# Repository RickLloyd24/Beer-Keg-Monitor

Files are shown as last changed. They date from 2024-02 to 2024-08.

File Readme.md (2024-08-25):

# Beer Keg Monitoring System

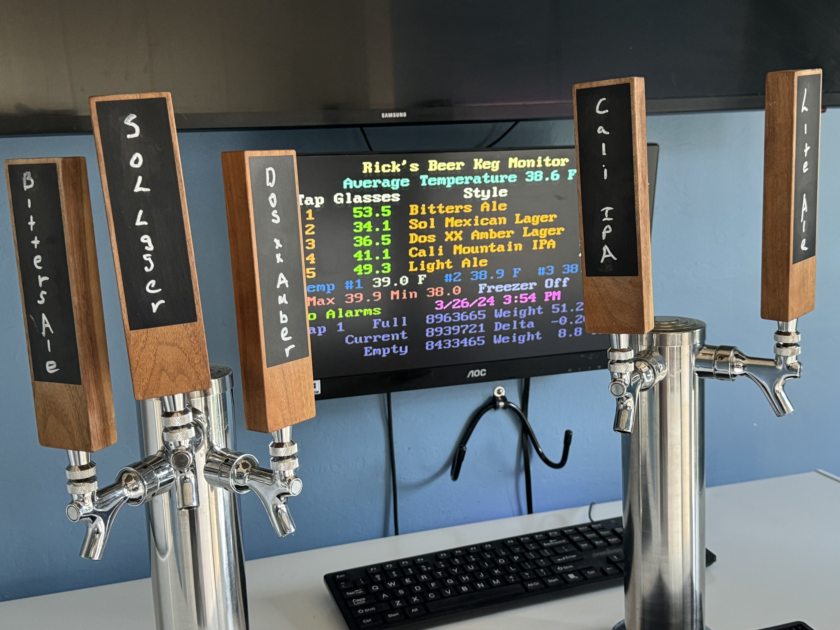
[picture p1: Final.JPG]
Build your own beer keg monitoring system that keeps track of how many
glasses of beer are left in each keg. The entire system costs less than
\$100 for 5 beer taps.

## Features:

- Tracks number of glasses of beer left.

- Controls Beer freezer temperature

- Monitors up to 8 beer taps.

- Temperature Stability +/- 0.75 degrees F

- Works with all DHT,  MCP9808 and/or DS18B20 Temperature Sensors

- - Up to 3 temperature sensors can be used.

- #NEW# Gets Time of day via WiFi and Network Time Protocol

- #NEW# Added CO2 Saver Support (See CO2 Saver Project)

- #NEW# Provides Redundant Power Supply Support

## Introduction

Currently there are two types of systems to measure how much beer is
left in the keg:

1) Flow measuring.

2) Weight of Keg.

Flow measuring systems are cheaper (6 taps about \$500) but they have
limited utility and you have to clean them every time you clean your
beer lines (every 6 weeks).

Weight of keg systems are none intrusive, but very expensive (\$1000 for
5 taps). They are not integrated with your entire system. This system
measures the weight of the keg but is low cost.

## Bill of Materials

The following is the bill of Materials for the entire system:

| Item | Qty | Description | Price | Total |
| ---- | --- | --- | --- | --- |
| 1 | 5 | Scale Plate | \$ 2.50  | \$ 12.50 |
| 2 | 5 | HX711 Load Cell Amplifier | \$ 2.00  | \$ 10.00 |
| 3 | 20  | Load Cell | \$ 0.80  | \$ 16.00 |
| 4 | 1 | PS2 Keyboard | \$ 5.00  | \$ 5.00  |
| 5 | 1 | VGA Monitor | \$ 10.00 | \$ 10.00 |
| 6 | 2 | DHT 22/AM2302 Sensor | \$ 3.33  | \$ 6.67  |
| 7 | 1 | ESP32 Breakout Board | \$ 13.00 | \$ 13.00 |
| 8 | 1 | ESP32 Development Board | \$ 8.50  | \$ 8.50  |
| 9 | 1 | VGA Breakout Board | \$ 7.50  | \$ 7.50  |
| 10 | 1 | PS2 Breakout Board | \$ 4.00  | \$ 4.00  |
| 11 | 1 | Relay | \$ 2.00  | \$ 2.00  |
| | | Total | | \$ 95.17 |

<style>
</style>

## Tools Required

- Soldering Iron (Amazon $10, Soldering Iron Kit - 9-in-1 With 5 Tips, Solder Wire)

- Connectors and Crimping Tool (Amazon $30, Kit with 1550PCS Male and Female 2.54mm Terminals)

- Multi Meter (Recommended Harbor Freight $7, 7-Function Digital Multimeter)

- Drill Motor

- Small Pliers, screw drivers

The following figure is a high level over of the whole project:

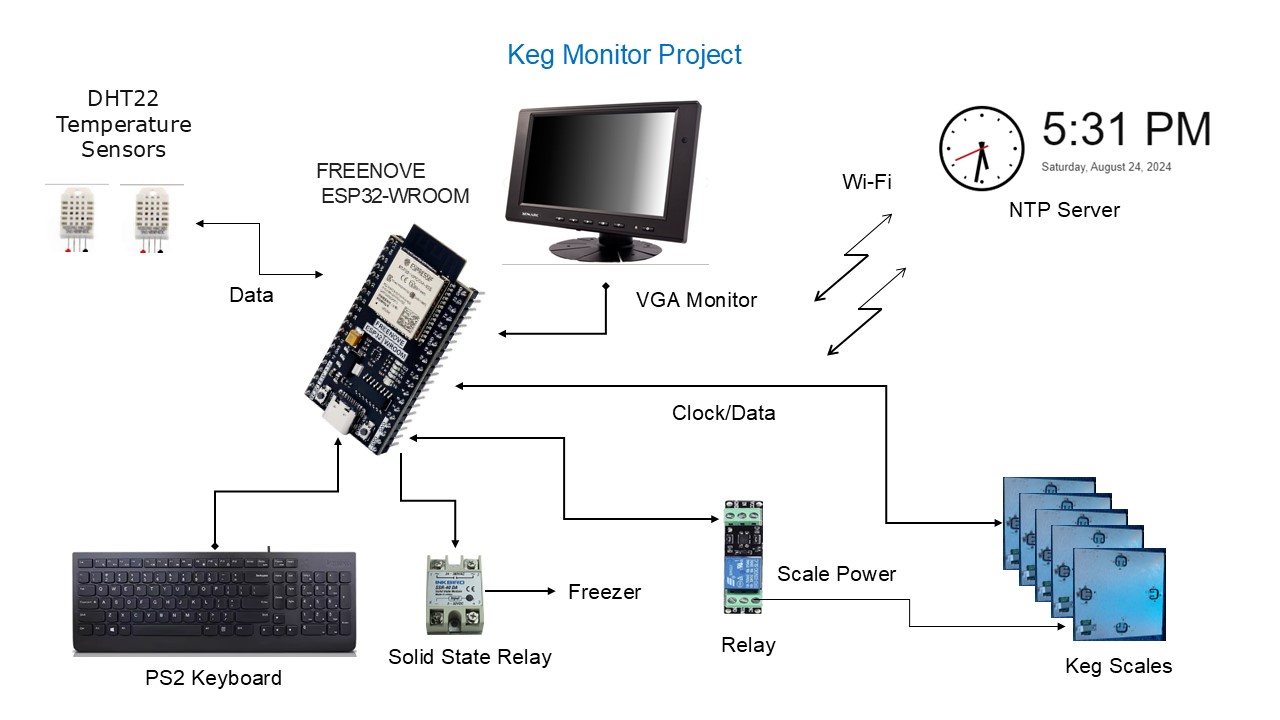
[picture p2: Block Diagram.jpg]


The data is displayed on the VGA monitor and input is via the keyboard.  A Solid State Relay (SSR) is used to control the freezer.  I replaced a standard relay with a SSR.  This relay is much more reliable and supports higher currents.  Upto  3 different temperature sensors can be used.  The time of day is received via Wi-Fi from an NTP Server.  A scale power relay is used to reduce false scale readings (discussed later).

## Theory of Operation

The theory of operation is quite simple. The data you need is:

1) Scale reading with nothing on the scale (Empty Scale Quanta)

2) Scale reading with a full keg of beer on the scale (Full Scale
   Quanta)

3) Scale reading of current keg (Current Scale Quanta)

4) Weight of a full keg (Full Keg Weight)

5) Weight of an empty keg (Empty Keg Weight)

The system automatically measures the first three items, all you need to
do is measure the full key weight and the empty keg weight. I just use a
bathroom scale.

Reading Per Ounce = (Full Scale Quanta – Empty Scale Quanta) / (Full Keg
Weight \* 16)

Current Ounces = (Current Scale Quanta – Empty Scale Quanta) / Reading
Per Ounce

Glasses = (Current Ounces – Empty Keg Weight) / 12 Ounces per glass

## Software

The software is in the software folder. 

## Hardware

Check out the hardware folders for all the intimate hardware details.

## Why a Keezer?

A Keezer is a chest **Freezer** converted to a **Kegerator** which is
commonly called a Keezer.

A Keezer has many advantages:

- They are more energy efficient.

- They have a lot of space for the cost.

- It is easy to access all the keg connectors.

- It is easy to install and remove the kegs.

Most freezers are not tall enough for the kegs with the fittings, so you
need to install a frame (collar) between the freezer top and the freezer
base. This is not very hard. You can find lots of articles on the
internet that describe how to do this.

The advantage of the collar is you do not have to drill through the wall
of the freezer to install taps, risking hitting a freezer coil. You can
also drill through the collar to bring in and out wires.

You should insulate the kegs from the bottom of the freezer to prevent
the beer from freezing and protect the bottom of the freezer. I used
padded vinyl plank flooring which worked great.

## Lessons Learned

1) Buy solid wire instead of stranded.  Much easier to work with.

2) Use an Ohm meter to check everything out.  It can save a lot of
   troubleshooting time. You can get one at Harbor Freight for just a
   few dollars. 

3) Buy the ESP32 Development Boards, instead of the UNO form factor
   boards (i.e. ESP32 D1 R32 or ESP8266 D1 R2).  Much easier to work
   with, better Wi-Fi, and faster.

4) If you need a lot of memory and pins use the ESP32-S3 development
   boards.

5) Use breakout boards with screw terminals, much easier and more
   reliable than the solder boards.

## HX711 Scale Sensor

I had a lot of trouble with the HX711 ADC sensor changing state. Periodically The scale reading would change to a completely different number and stay in this state. The readings were still very consistent in this false state. Powering the system On/Off would restore the HX711 ADC to the correct state.

I was able to determine the cause of this problem was power transients. I confirmed this by powering the scales from a battery for several days and no transients occurred.

To fix this problem a scale power relay was added. Every time the freezer is turned On/Off or the CO2 solenoid is turned On/Off the scales are powered off before the event. After the event the scales are powered back on. This finally solved the problem.

The other advantage of this solution is, if another source caused the power transient, the scales will eventually be turned Off/On and read the correct value.

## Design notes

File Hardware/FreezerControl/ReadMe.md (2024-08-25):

# Freezer Control Relay

The Freezer Control Relay is used to turn On/Off the freezer.

## **Relay Specifications**

The following are the specifications for the relay.

- Input: DC 3-32V;
- Output: AC 24-380V, 40 amps
- Number of switches: Infinite

The relay supports currents up to 40 amps and the relay activation works down to 3 volts.  A GPIO output can be used to drive the relay. The approximate current at 3.3 volts is 8.5 milliamps. The maximum drive current for an ESP32 GPIO is 40 ma, with 20 ma recommended maximum. So, this relay is a good, reliable choice. The SSR also has a resistance of about 3 ohms with a 3.3-volt drive that reduces the surge current.

The freezer I use was an Insignia™ - 10.2 Cu. Ft. Chest Freezer. The startup current is 21.4 amps and the on current is 2.0 amps. This relay has handled the startup current fine. 

Initially I used a small 10-amp relay. The relay failed in the "On" state after about 6 months which froze my beer.  I think because of the high inrush current.  A mechanical relay has a life expectancy of about 1 million activations. Under normal operation as a freezer controller the relay will last about 5 - 7 years. However, Solid State Relays (SSR) have an infinite number of switches. A SSR will not last forever, but it fails for reasons other than switching.I strongly recommend the SSR relay because it is more robust and more reliable. You may also consider the redundant relay that I talk about in the next section.

## **Schematic**

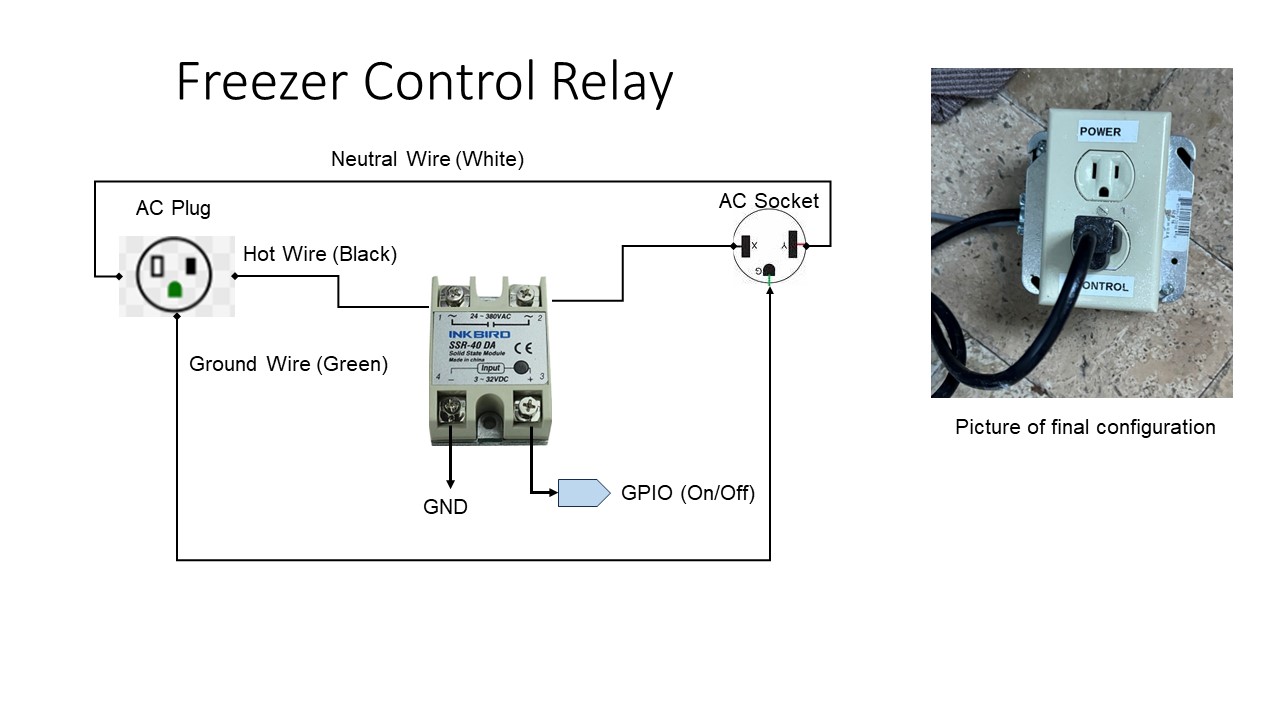
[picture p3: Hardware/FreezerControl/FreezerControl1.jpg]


The above schematic provides an overview of the connections. I included a picture of my final product. I got the line cord off a food blender that was broken. The line cord has 16-gauge wires.  The plug and the box were pieces I had laying around. The relay is enclosed inside the electrical box. The plug in the box goes to the freezer.  

## **Redundant Relay Configuration**

### **Background**

SSRs can fail in either the open or closed position. Since I have about $500 worth of beer in my freezer, I wanted a redundant relay that would still work if the primary relay failed in either the open or closed position. the following describes my solution.

## **Overview**

The redundant relay concept is shown in the following figure:\

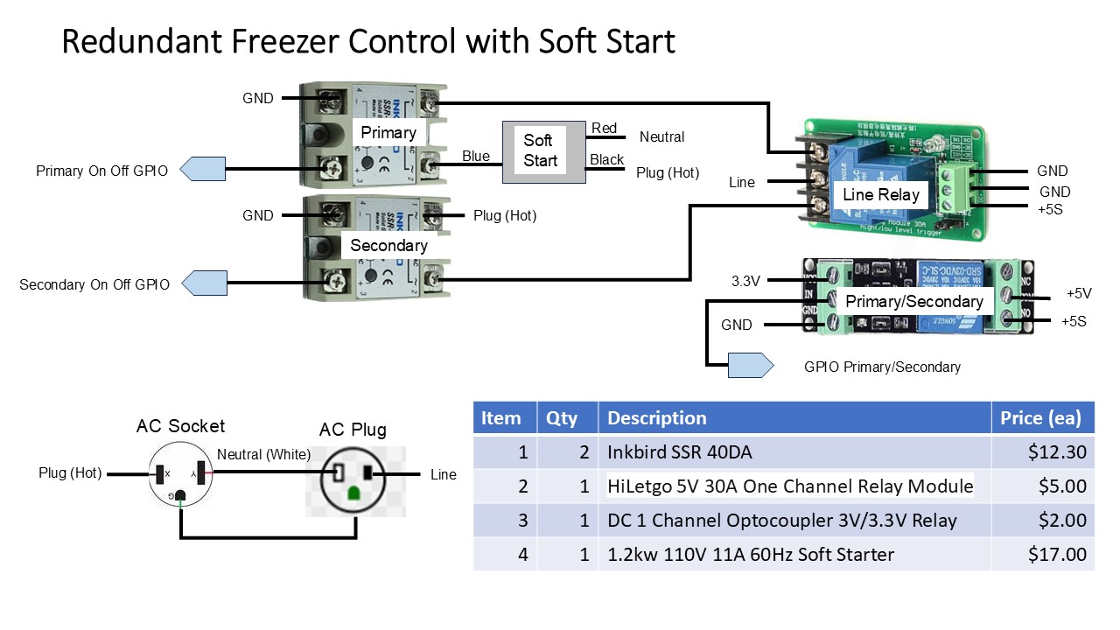
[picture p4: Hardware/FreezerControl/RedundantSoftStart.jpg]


There are primary and secondary circuits in the design. When primary is on (LOW) no components are powered on when the freezer is Off.  When the Primary GPIO On/Off signal is HIGH the SSR switches on. The current drain is about 8.7 ma, which is about half of the  recommended maximum. The GPIO On/Off signal is HIGH about 25% of the time in the summer.

A switch to the secondary circuit occurs when the freezer temperature is below 32 degrees or above 40 degrees. Once switched to the secondary the only way to get back to primary is to reset the ESP32 board or enter a command.

The switch to Secondary only occurs when the GPIO On/Off signal is in the off position, so no AC current is flowing. When the GPIO Primary/Secondary signal goes HIGH, the Primary/Secondary relay activates the +5S signal which activates the Line Relay. The line relay now sends the AC power to the secondary SSR. When the secondary circuit is active the Secondary On/Off GPIO signal is used.  I wanted a relay with big contacts for the Line Relay and I could not find one that worked on 3.3 volts. The Primary/Secondary relay is included just to provide 5 volts to the Line Relay. You can eliminate the Primary/Secondary relay if you want to use a 10 amp relay.

The Secondary circuit is tested everytime I need to change a keg in the freezer or I clean the beer lines.  That way I know the Secondary circuit is good.  After the freezer gets back to the desired temperature, I switch back to Primary.  You can tell which circuit is active on the main display.  There is either a "P" or "S" next to the freezer status.

This diagram includes a soft start circuit to reduce the freezer on current.  It seemed to help some but I am not sure it is worth the extra cost and is another component that can fail.

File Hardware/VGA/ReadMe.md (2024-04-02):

# VGA Interface

For this project I selected a VGA monitor for my local display. VGA monitors
are large and easy to read for my guests. They are also readily available and
cheap. I got mine free at a garage sale. They were closing up and the monitor
was still there, so they gave it to me. I also bought a VGA monitor at a thrift
store for 10 dollars.

## VGA Interface Schematic

The following is the schematic for the VGA interface:

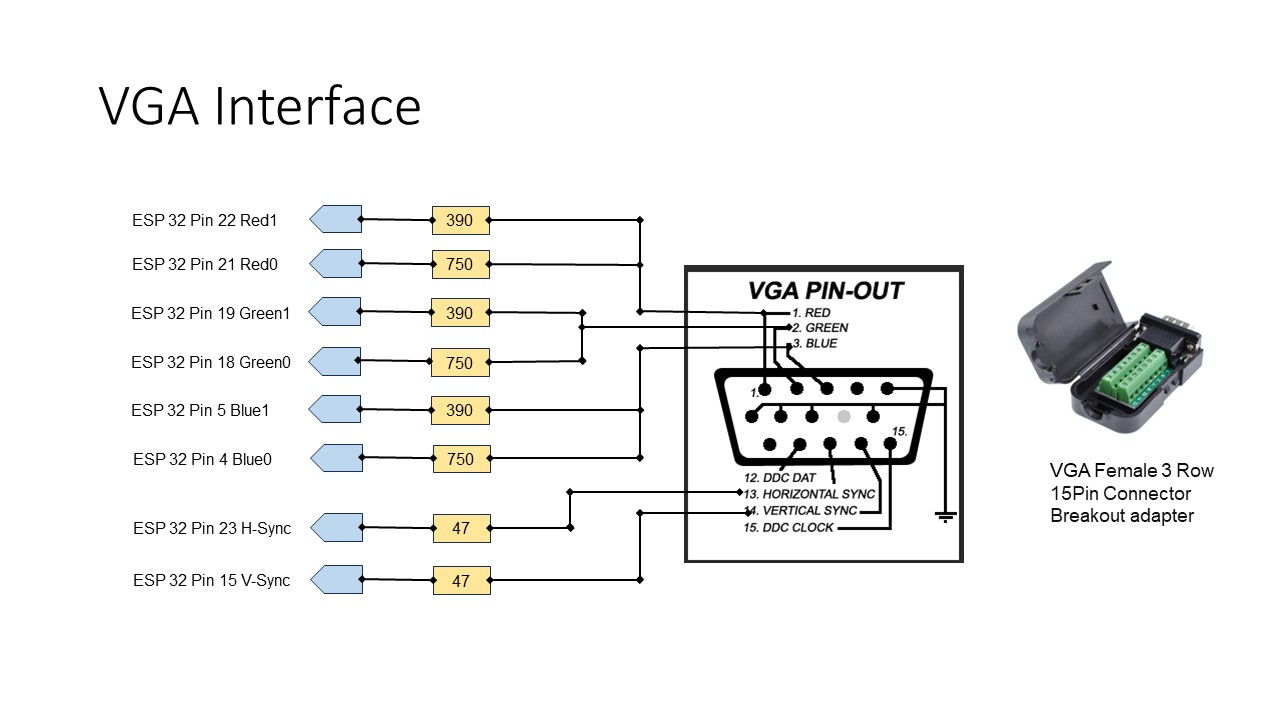
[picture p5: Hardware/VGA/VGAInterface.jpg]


The resistors for the RGB signals should have approximately a  2 to 1 ratio. The 47-ohm resistors are for impedance matching.

With this configuration you get 64 colors. 

## Software

For this project I used the FabGL Graphics Library for ESP32.  This library is great!  I used the same library for my keyboard interface.  The library overview is at the following link  [www.FabGL.com](http://www.fabgl.com/)  and is also available on Github.  I used the default pin numbers as defined in the library.

There is a **VGATest** program that displays all 64 colors and can help you test the VGA interface.  The following is a sample of the test display showing all 64 colors.

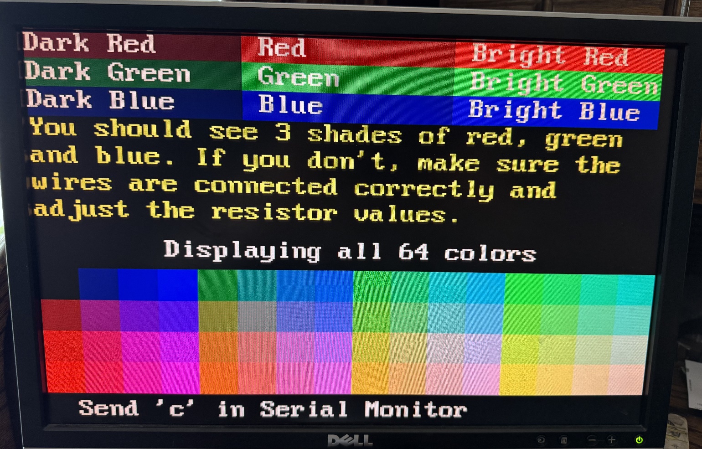
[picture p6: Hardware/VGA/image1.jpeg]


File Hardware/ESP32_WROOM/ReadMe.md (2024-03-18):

# **FREENOVE ESP32-WROOM Board**

For this project I selected the FREENOVE ESP32-WROOM developement board.  The main reason is the breakout board that is available for this board.  The breakout board is great.  I prefer to use a Arduino power supply instead of powering board from a type C USB connector.

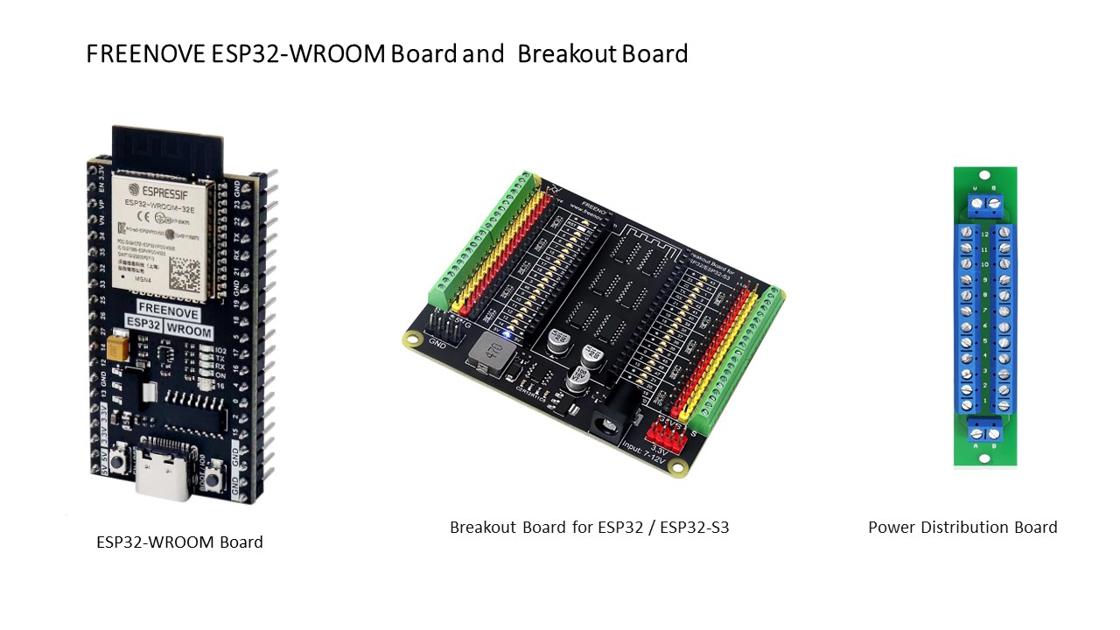
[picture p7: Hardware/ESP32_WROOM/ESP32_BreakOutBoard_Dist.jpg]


## ESP32 Breakout Board

Breakout Board Features:

- •Compatible models -> Freenove ESP32 / ESP32-S3 series. (Note: Boards from other brands are not compatible due to different pinout.)

- •GPIO status LED -> LED on if GPIO outputs/inputs high level, LED off if GPIO
  outputs/inputs low level.

- •Independent LED -> The status LED is driven by the chip instead of the GPIO so the GPIO will not be affected.

- •Power circuit -> Provide multiple 5V and 3.3V power outputs. (5V output up to 3A
  with external power supply.)

- •Terminal block and header -> Connect to all GPIO headers 

## ESP32-WROOM

The ESP Development board has:

- 32 bit processor that runs at 240 MHz

- 4 MB Flash and 520 KB of SRAM running at 80 MHz

- Wi-Fi and Bluetooth Interfaces

- Onboard RGB LED and Green LED

- Onboard Code Uploader

The ESP32 includes

- 8 Analog-to-Digital Converter (ADC) channels

- 3 SPI interfaces

- 3 UART interfaces

- 2 I2C interfaces

- 16 PWM output channels

- 2 Digital-to-Analog Converters (DAC)

- 2 I2S interfaces

- 10 Capacitive sensing GPIOs

The ADC (analog to digital converter) and DAC (digital to analog converter) features are assigned to specific static pins. However, you can decide which pins are UART, I2C, SPI, PWM, etc – you just need to assign them in the code. This is possible due to the ESP32 chip’s multiplexing feature.

## Power Distribution Board

I use these boards for my 3.3 Volt power and ground distribution.  There are not enough pins the ESP32 for all the power and ground signals.  These little boards make distributing the power and ground very easy.

## FREENOVE ESP32 Pin Out

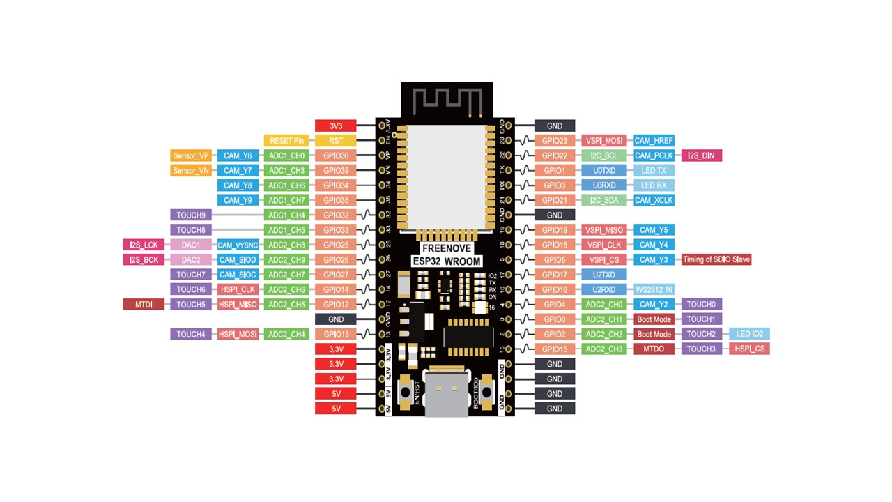
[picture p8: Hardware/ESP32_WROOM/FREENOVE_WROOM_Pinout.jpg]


##

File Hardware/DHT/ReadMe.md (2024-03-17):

# DHT22/AM2302

The Digital Humidity and Temperature (DHT)  Sensor Module is compact and easy to use module.  

## Features:

- Main Chip: AOSONG AM2302 High Sensitive Temperature Humidity Sensor
- Single-bus digital signal output, bidirectional serial data
- Temperature range: -40 to 80 degree celsius, 
- Temperature measurement accuracy: +/- 0.5℃ degree celsius
- Humidity measuring range: 0~100%RH, 
- Humidity measurement accuracy: ±2%RH

## Specifications

- Power supply 3.3-6V DC

- Sensing element Polymer capacitor

- Operating range humidity 0-100%RH; temperature -40~80 Celsius

- Accuracy humidity +-2%RH(Max +-5%RH); temperature <+-0.5 Celsius

- Resolution or sensitivity humidity 0.1%RH; temperature 0.1 Celsius

- Repeatability humidity +-1%RH; temperature +-0.2Celsius

- Humidity hysteresis +-0.3%RH

- Long-term Stability +-0.5%RH/year

- Sensing period Average: 2 seconds

## Software

The software will work with any DHT sensors (DHT11, DHT21, DHT22, AM2301, or AM2302). You can use upto 3 sensors (any mix of MCP9808 and DHT sensors). The "constants.h" file is edited to select the number of sensors and the type of sensors used.

I tried multiple DHT sensor libraries.  They either were unreliable (sensor temperature got stuck) or they were blocking which caused the display to blink when the sensor was read.  To solve this problem I wrote my own library <DHTSimple.h>.  This library is avalible on GitHub.

The DHT sensors can be connected to available GPIO pin.  The pin numbers are defined in the "constants.h" file.  If MCP9808 sensors are installed, the sensor numbers will be assigned to these devices first.

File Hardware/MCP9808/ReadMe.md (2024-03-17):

# MCP9808 Precision Temperature Sensor

This MCP9808 digital temperature sensor is low cost temperature sensor with a typical accuracy of ±0.25°C over the sensor's -40°C to +125°C range and precision of +0.0625°C.   It has a wide voltage range of 2.7  to 5.5 volts.  You can typically buy them for about 6 dollars.   The following is a picture of the typical device.  The device works on the I2C bus that is explained in the next section.

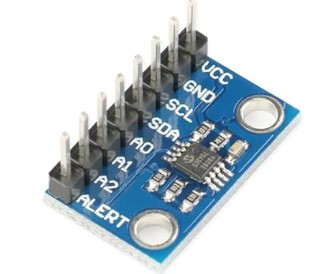
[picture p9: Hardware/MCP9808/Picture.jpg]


## I2C Bus

The I2C bus is a standard **bidirectional interface** that uses a controller, known as the master, to communicate with slave devices. A slave may not transmit data unless it has been addressed by the master. Each device on the I2C bus has a specific device address to differentiate between other devices that are on the same I2C bus.  The I2C bus can support 255 different addresses with a two wire interface.

All Arduino compaitible boards support the I2C bus.  The MCP9808 has 3 address pins so you can connect up to 8 on the I2C bus.  The base address 0x18.

The I2C bus is supported by the Arduino Wire library.

## MCP9808 vs DHT Sensors

I decided to add the capability to use either Digital Humidity and Temperature (DHT) or  MCP9808 sensors.  I found that the DHT22 sensors had temperature biases upto 2 degrees and they seem to drift.    The following figure compares the MCP to the DHT22.

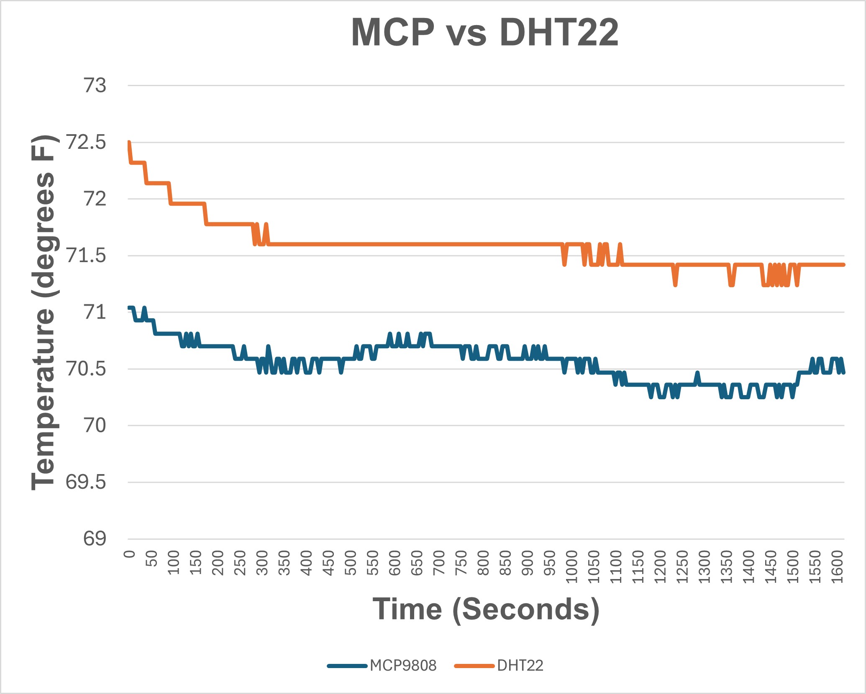
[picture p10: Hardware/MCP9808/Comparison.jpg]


## Implementation

I ran five wires to each sensor (+3.3V, Gnd, SDA, SCL and A0).  On one sensor A0 was connected to 3.3V and the other sensor is connected to GND.  The addresses of the two sensors are hard wired to 0x18 and 0x19.  The following is a picture of the wired sensors.  I found that the ground wire had to be run to 0x18 sensor (sensor #1) to get reliable readings.  In the picture these sensors are generic sensors.  On Adafruit sensors the Alert pin is where the A0 pin is.  For the Adafruit sensors I used a 4 pin connector and ran a single wire to the A0 address line.

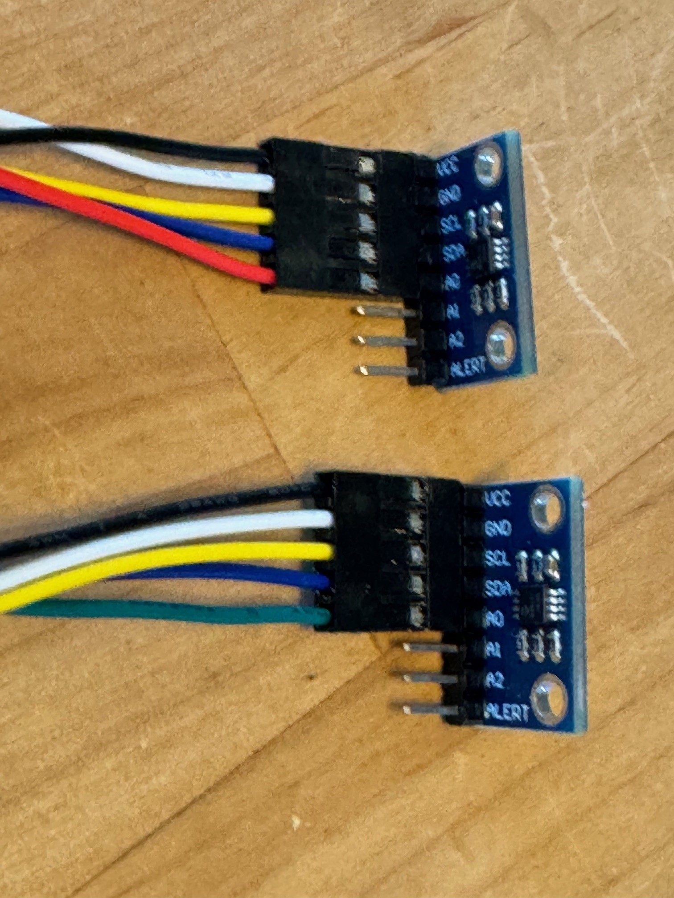
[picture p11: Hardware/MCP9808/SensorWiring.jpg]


Because the IC2 bus runs at a high rate (100 kHz)  the SDA and SCL wires should be kept to about a foot or less.  The other wires can be longer.

## Software

You can use upto 3 sensors (any mix of MCP9808 and DHT sensors). The "constants.h" file is edited to select the number of sensors and the type of sensors used.

The SDA and SCL pins are also defined in the "constants.h" file.  The SCL pin is 13 and the SDA pin is 14, but these can be assigned to almost any GPIO pin.

The MCP9808 sensors are assigned sensor numbers first.  For example if you have 2 MCP9808 sensors and 1 DHT sensor, Sensor #1 and Sensor #2 are the MCP9808 and Sensor #3 is the DHT sensor.

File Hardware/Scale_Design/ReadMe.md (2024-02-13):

# Scales

For the scale plate I used Aluminum Composite Sign Panel sheet.  The sheets are 1/8 inch thick and come in a variety of sizes.  The most common is 12 inches by 24 inches.  You can use standard wood cutting tools to work with the plates.



I made two sizes of scale plates.  9.25 inches for Corny and 1/6 Barrel kegs. 12.125 for the Slim 1/4 Barrel.

## Schematic

The following is a schematic for one load cell:

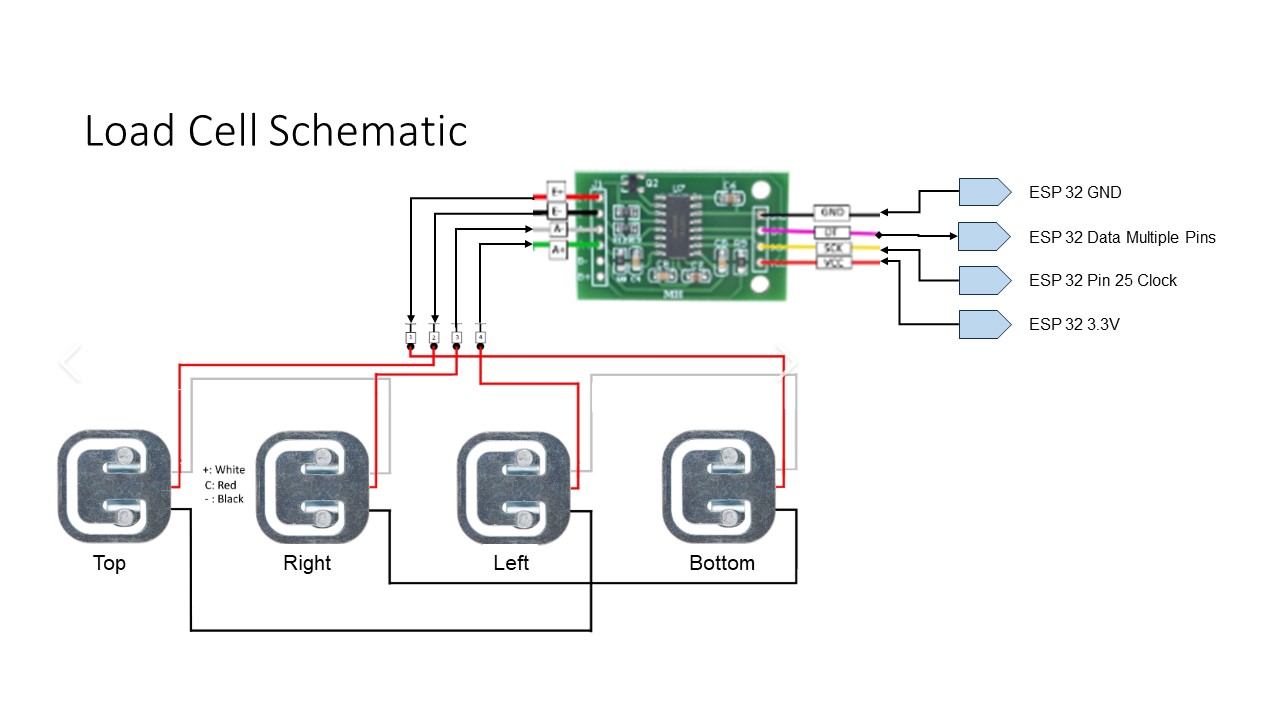
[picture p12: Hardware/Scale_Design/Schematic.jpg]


The following is the Schmatic for multiple scales:

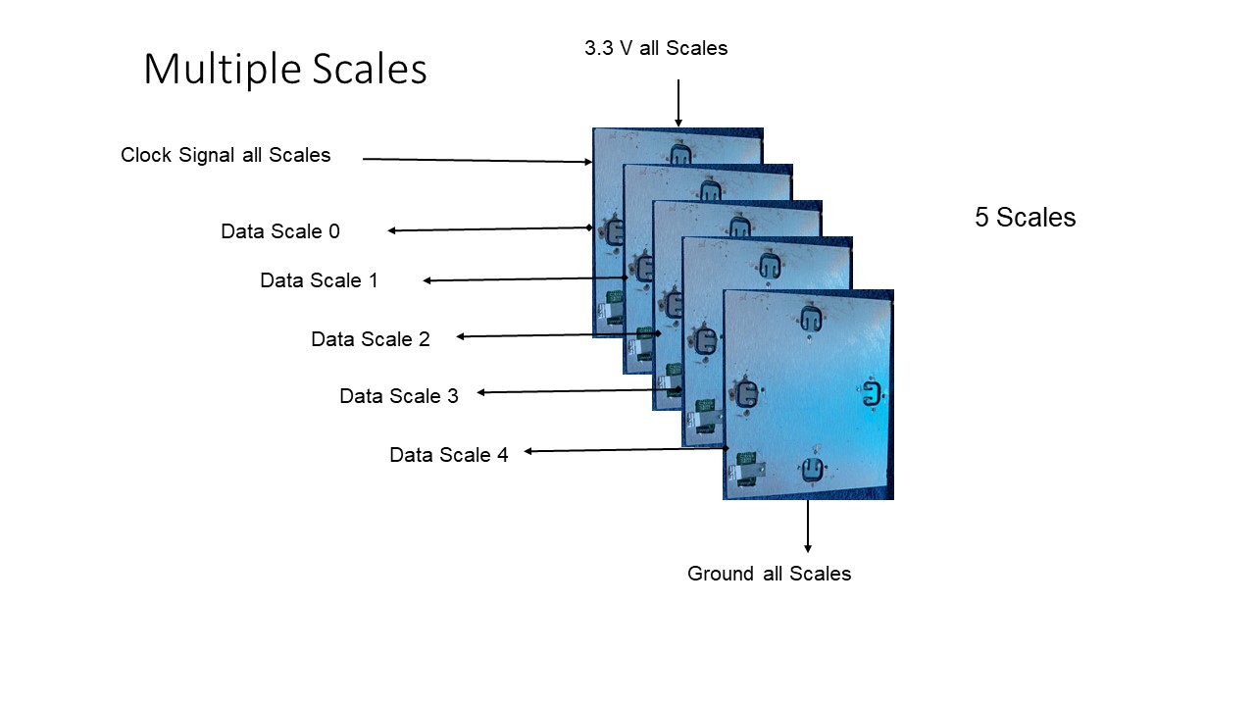
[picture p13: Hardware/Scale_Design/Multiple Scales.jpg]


## Making the Scales

To make the scales, I used a table router and a table saw.  The following figure illustrates how to make the plates.  The plates size depends on which keg you plan to use.  The holes are for the strain gauge and on the center line of the plate.  I made them holes so you can align the strain gauge in the slot.  The route area is for the HX711 board.  You route out the area leaving a 1/16 inch top.  You cut a through area for the pins to go through the board.

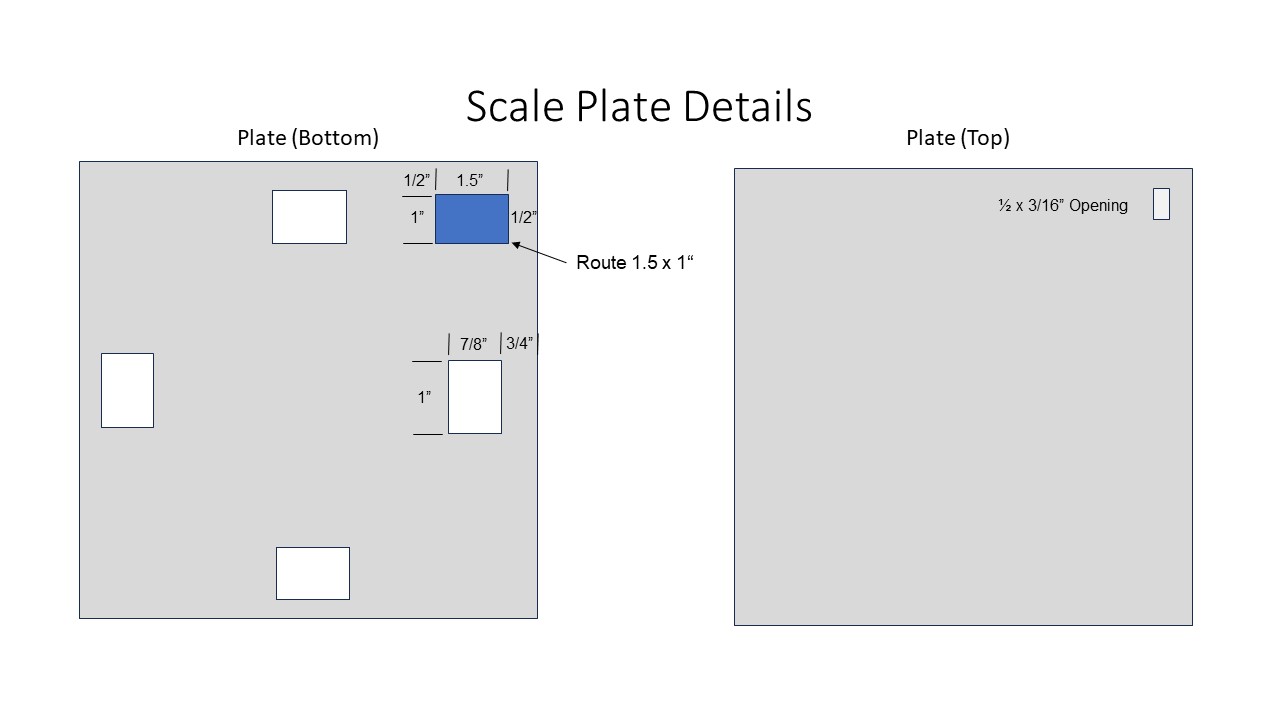
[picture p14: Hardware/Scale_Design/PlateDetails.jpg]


They hold the strain gauges and HX711 boards in place I made some retainers out the scrap material.  On the strain gauge retainer, you route out an area and again leave 1/16 inch top material.  The retainer only keeps the strain gauge from moving.  All the keg weight is supported by the plate and the strain gauge.  I also made a little retainer to hole the HX711 board in place.  

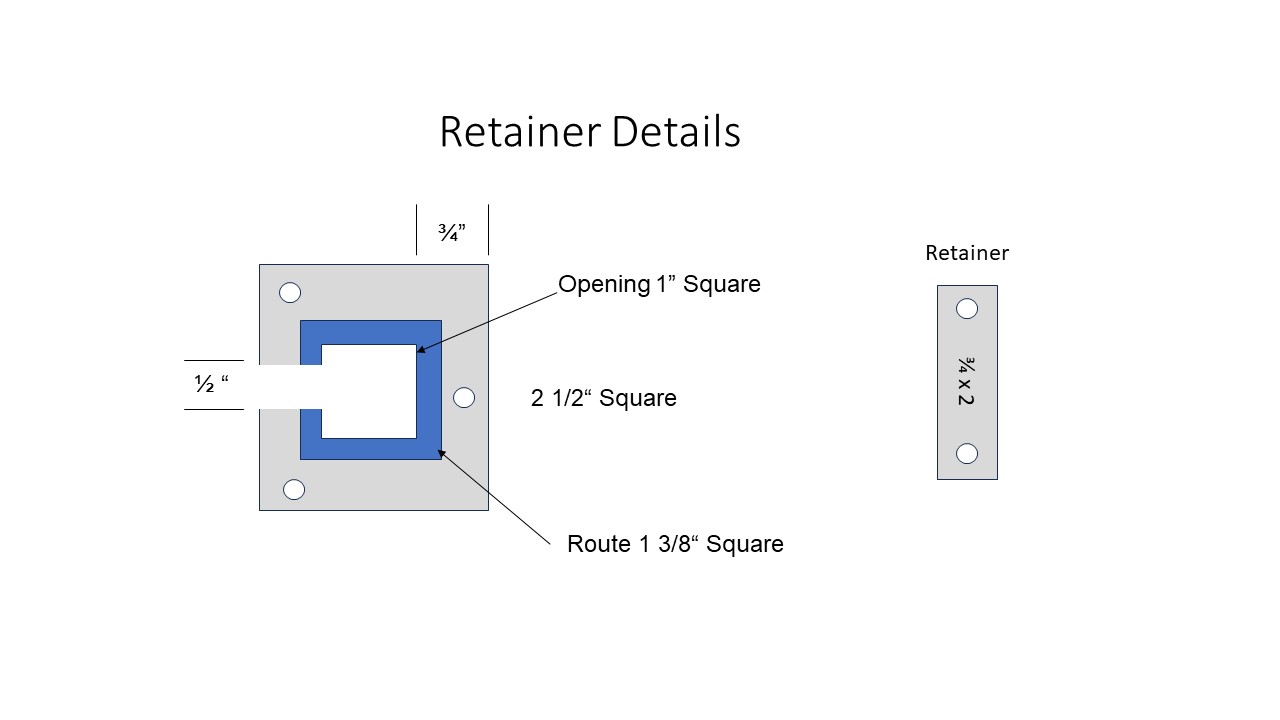
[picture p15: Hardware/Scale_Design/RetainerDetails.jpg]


To hold the retainers in place  I used 1/4-inch flat head machine screws.  I drilled and tapped the plate to hold the screws.  You can also use sheet metal screws, so you don't have to drill and tap. The following picture is the final product.  I just taped the wires to the plate on the bottom.

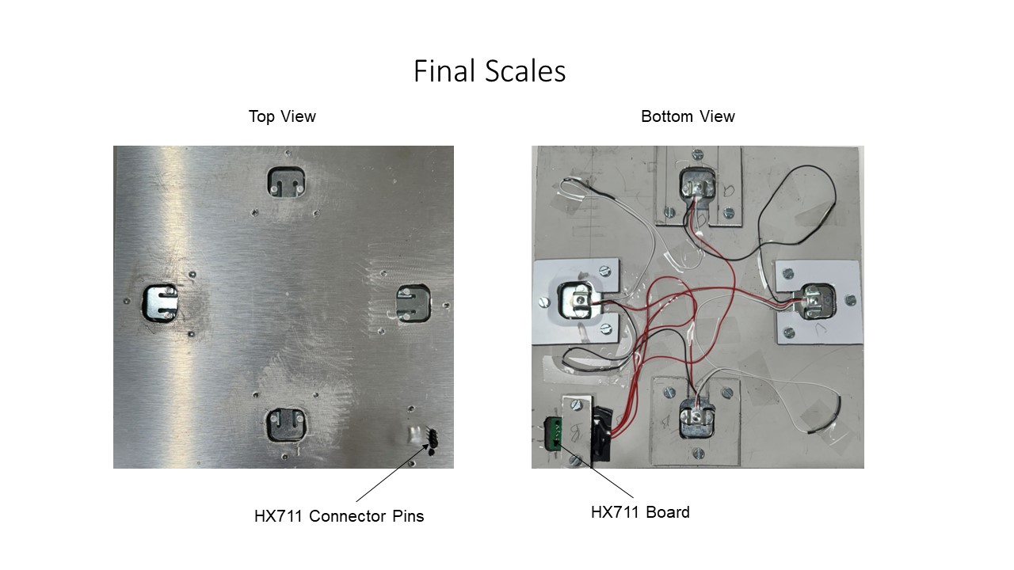
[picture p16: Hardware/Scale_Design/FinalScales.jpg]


If you don't have a router table you can cut the holes in the plate and use sheet metal screws to hole the strain gauges and HX711 board.  The following figure is an example of this method.

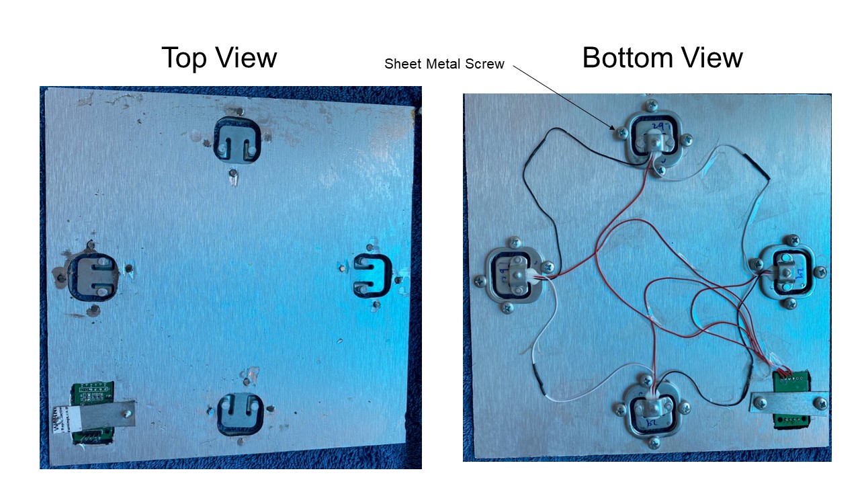
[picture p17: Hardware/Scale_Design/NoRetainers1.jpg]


## Keg Holder

I made keg holders for the kegs. The keg holders protect the HX711 connector from getting squashed and provide a hard surface for the strain gauge to sit on.  My freezer bottom was soft and strain gauge pressure point went right into the bottom.  The following figure illustrates the keg holder.

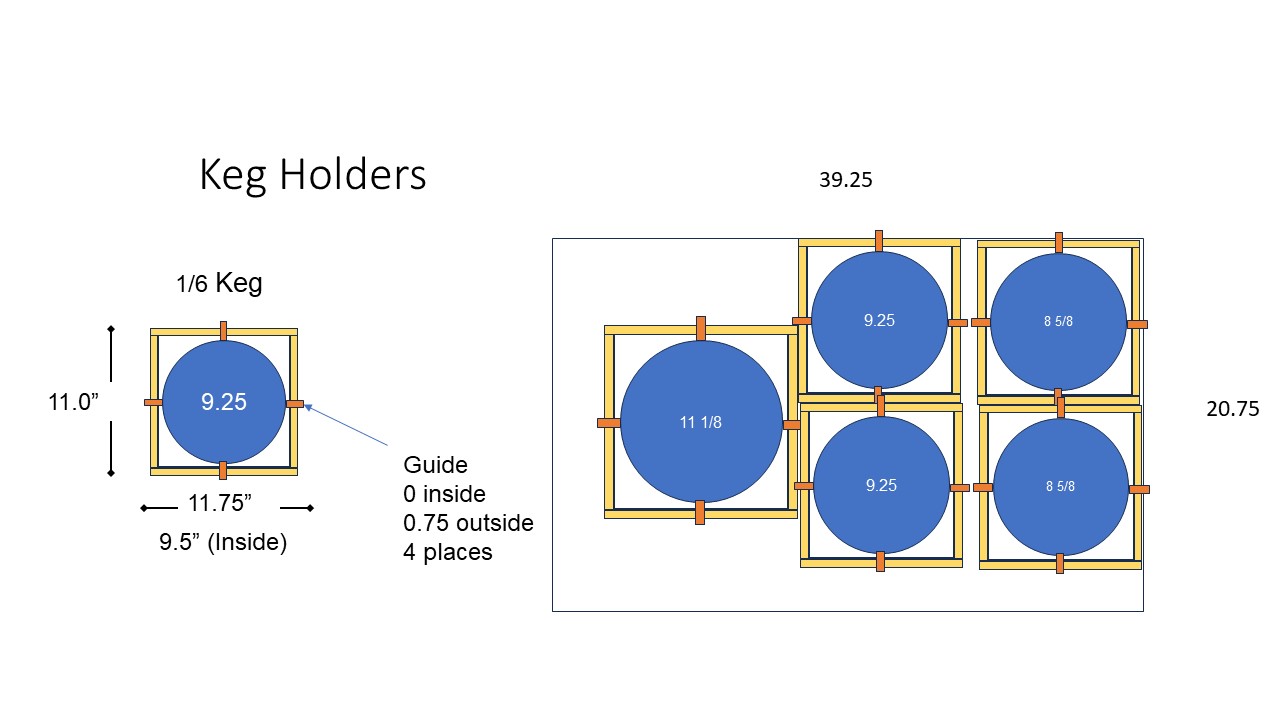
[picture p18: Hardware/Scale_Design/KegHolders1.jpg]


The keg holder uses 1x2 lumber for the frame with a hard plate on the
bottom. I used vinyl plank flooring on the bottom. It is completely waterproof,
has a nice rubber backing for the bottom and has a very hard surface. The
bottom is just nailed to the frame. The figure on the right shows my final 5
keg configuration.

I installed guides to help when I installed the keg. It turns out they
really don't help and are unnecessary.

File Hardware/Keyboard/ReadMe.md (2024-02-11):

# Keyboard

I selected a PS2 keyboard for this project because they are very easy to
interface. You can normally find PS2 keyboards at garage sales and thrift
stores, but they are getting harder to find. You can tell it is a PS2 keyboard
by the distinctive round PS2 connector. For awhile they made PS2 compatible
keyboards with a USB connector, but unless the keyboard specifically says PS2
compatible it will not work. If you can't find a used PS2 keyboard, new ones
are available on Amazon for about 20 dollars.

## Keyboard Schematic

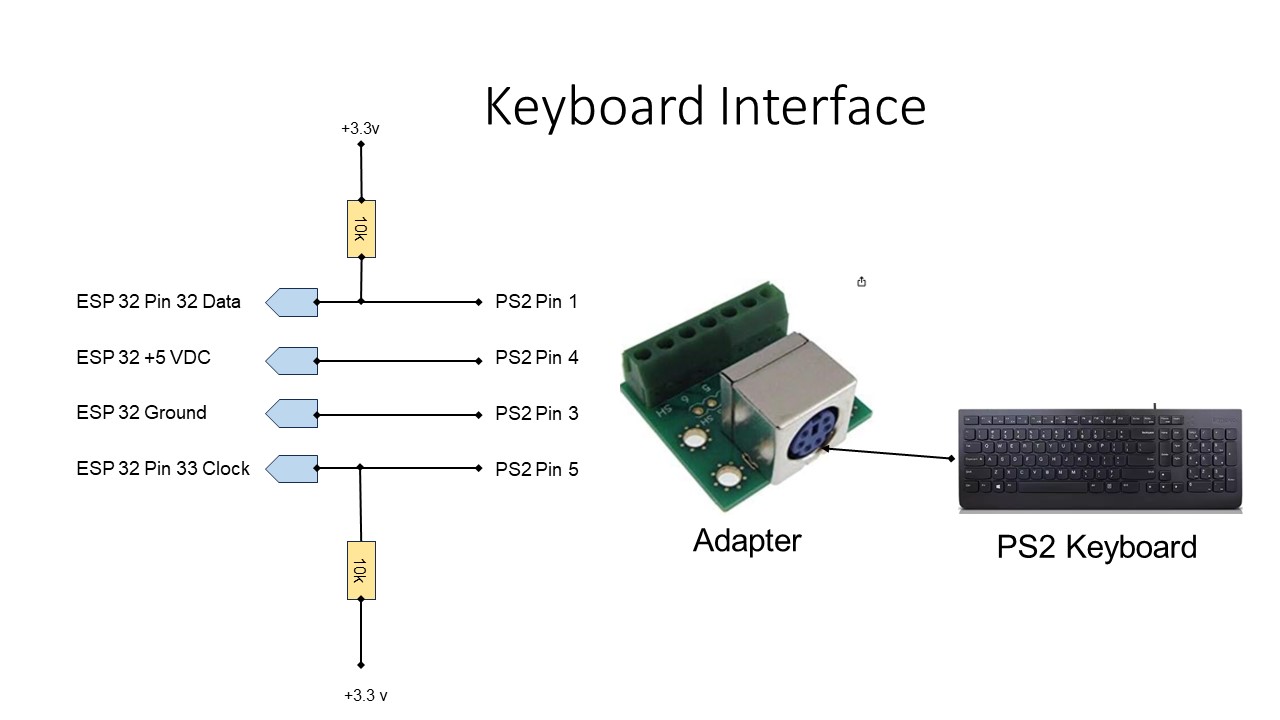
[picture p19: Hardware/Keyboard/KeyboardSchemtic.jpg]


<style>
</style>

The PS2 keyboard requires 5 volts to operate and the ESP32 operates on
3.3 volts. So you need to make sure that the keyboard is wired to 5 volts and
the pullup resisters are connected to the 3.3 volt supply. The PS2 output is an
open collector interface.

PS2 breakout adapters like the one shown in the schematic are available,
but can be hard to find. There are USB to PS2 adapters readily available, so
you can use a USB breakout adapter instead.

I looked at using a USB keyboard, but you need a USB to TTL adapter, and
they were as much money as the PS2 keyboard.

## Software

For thie keyboard again I used the FabGL Graphics Library for ESP32. This library is great!  The library overview is at the following link [www.FabGL.com](http://www.fabgl.com/)  and is also available on Github. I used the default pin numbers for the keyboard from the library.

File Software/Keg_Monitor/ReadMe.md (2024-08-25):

# Keg Monitor Program

The Keg monitor program controls the freezer temperature, measures how
many glasses of beer are available and provides a display with all the
beer information you need. 

The program runs on the FREENOVE ESP32-WROOM development board
(Keg_Monitor_RevX.X.ino). Arduino compile information is included on the
first line of the file.

The program also interfaces to a Wi-Fi board via a serial interface. 
You can use the program without this interface, but you will not be able
to send emails or text messages if something is wrong.  You can manually
input the time of day to get the number of days the beer has been
kegged.

The program display is a standard VGA display. I set the resolution to
40 characters by 15 lines, so it is easy to read from a distance.  The
following section describes the display.

# Main Display Overview

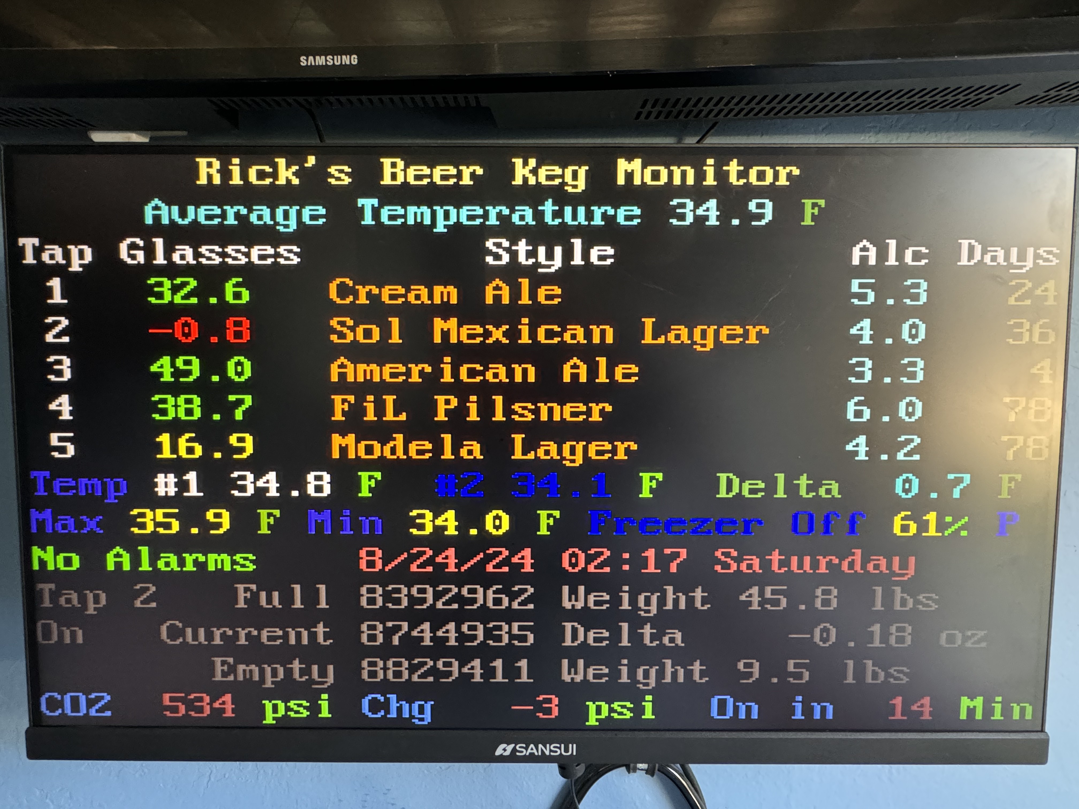
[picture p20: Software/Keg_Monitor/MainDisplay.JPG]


The first line is the Name of your system.  I called mine Rick’s Beer
Keg Monitor.

The second line is the average temperature.  This is the average of 180
samples or 30 minutes.

The third line is the titles for the columns.  The first column is the
Tap number, the second column is the number of glasses remaining, the
third column is the name and style of the beer, the fourth column is the
percentage of alcohol, and the last column is the number of days the keg
has been in freezer.  The Glasses column changes colors depending on how
many are left.  Less than 30 is yellow and less than 10 is red.

The 9th line is the current temperatures.  The highlighted temperature
is the sensor currently being used. 

The 10th line displays alarms and time of day.  If there are not any
alarms the display will show “No Alarms” in green.  If there are alarms
the display will show the number of alarms in red.  Next to the alarms
is the time of day.  If the Wi-Fi module is connected the time of day is
automatically displayed.   If the area is blank, you can manually input
the time of day.

The next three lines provide scale information.  The first line is Tap
number, the scale quanta value for a full keg and the weight of the keg
when it was full.  The next line shows the current quanta value and the
change in ounces between two consecutive readings.  If the scale is
working properly this should be a small number, unless you are pouring a
beer.  The last line shows the empty scale (nothing on the scale) quanta
value and the weight of an empty keg.

The last line is the CO2 status information. The first field is the
current CO2 pressure. The next field is the change in pressure during
the last hour. If the change is greater than 100 psi you may have a
leak. The last field is how many minutes before the CO2 valve turns on
agan.

With the main display being displayed pressing a key will have the
following effect:

- Key a – Displays the current alarms.  Pressing the Esc key will clear
  the alarms and return you to the main display.

- Key 1-5 – Pressing a number key will display the information for the
  appropriate tap in the bottom three rows.  If you select the tap
  before you pour you can watch the ounces change.

- Key c – Clears the Minimum, Maximum and average temperatures.

- Key s – Opens the scale display window.

- Key p – Opens the CO2 plot display window

- Key Esc – Opens up the command menu.

**Command Menu**

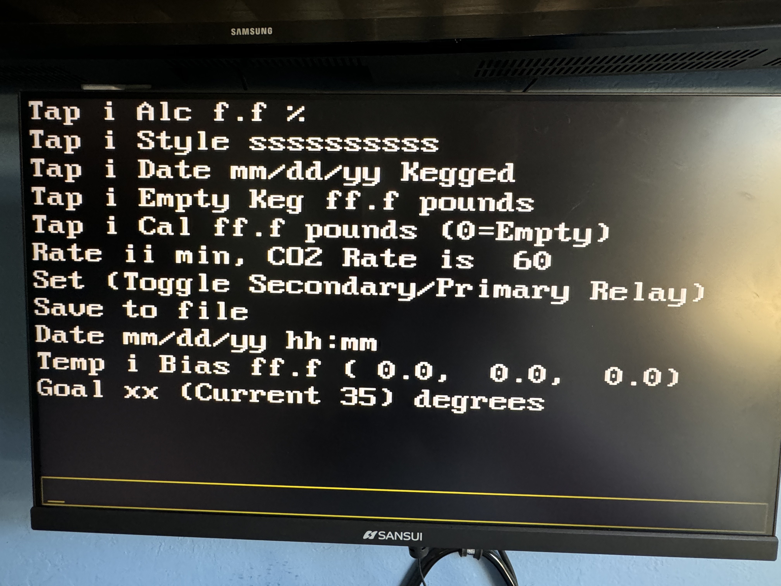
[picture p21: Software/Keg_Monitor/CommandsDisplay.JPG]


With this display you type the command to execute.  As you type, the
letters appear on the bottom of the display in the box.  You can hit
backspace to clear what you typed.  To exit this display hit the Esc
key.

The first five lines are for entering keg information.  Type the Tap
number and the information.  The information is alcohol percentage,
Style or name of beer, date the beer was kegged or installed in the
freezer and the weight of an empty keg.

The 5th line is for calibrating an empty keg and full keg.  If there is
not anything on the scale the main display should show the number of
glasses at about minus 13.  If not calibrate the scale with a weight of
0.  Put the full keg on the scale and enter the weight of the full keg
to calibrate.

The next line sets the CO2 valve rate. 0 turns it on continuously and 99
turns it off.

The nest line sets either the primary or secondary relay.

Save to file, saves the current information to file.  Don’t forget to
Save when you have input information correctly.

Date is used to input the current date and time when you don’t have the
Wi-Fi board connected.

The “Temp i Bias” line is to input the bias on the temperature sensors. 
The line shows the current bias value.

The Goal is the temperature you want your freezer to be.  The DHT
sensors can have a bias.  I have had some sensors that had a bias up to
2 degrees.  Before you set the goal too low make sure the bias and
temperature are correct.  Freezing beer is BAD!  I found that 36 degrees
is safe, and the beer still tastes nice and cold.  Refrigerators are
normally 40 degrees.

## CO2 Saver

When you press ‘p’ on the main display the following plot is displayed.

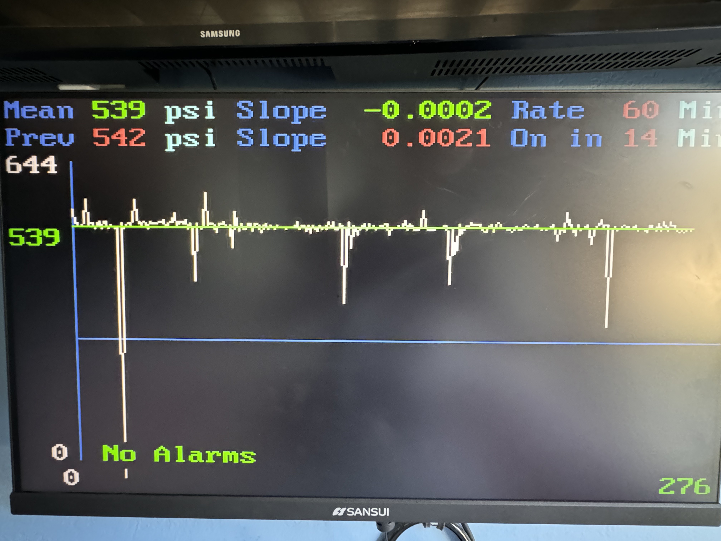
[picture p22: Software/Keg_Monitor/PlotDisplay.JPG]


The top row shows the current average pressure, and the slope of the
line fit to the raw data. The Rate is the current on rate.

The next line is the previous mean and slope. The last field is when the
CO2 valve will turn on.

The rest of the display is the plot. The left is the X-axis in psi and
the bottom is the y-axis in number of samples. The green values and line
are the linear regression fit the raw data. The white is the raw data.

## Setup

All the setup is done by editing the “Constans.h” file. In my
configuration all the available GPIO pins are used. I use two MCP9808
temperature sensors that use the SCLpin and SDApin. If you want to use
different temperature sensors you need to change the pin numbers. So for
example, if you are using two DHT Type 2 sensors you need to change the
DHT1Pin to 13 and the DHT2pin to 14 and change SCLpin to -1 and SDApin
to -1. You have to keep all the pin names for the program to compile.

Another example, if you are not using the CO2 Saver, you set CO2Saver to
false. Now pin 0 and pin 35 are available to use, but you have to set
CO2ValvePin to -1 and CO2PressurePin to -1.

If you are using Wi-Fi to get time of day, you have to set ssid to the
name of your Wi-Fi network and password to the password of your network.
If you don’t live on the west coast you have to change the gmtOffset_sec
to your time zone.

## Software Files

The software is divided into files. The files contain functionally
similar functions.

### “Constants.h”

This file contains the temperature sensor configuration information,
GPIO pin assignments, color constants, alarm numbers and other global
constants. I made this a separate file to reduce clutter in the main
program. I think the comments in the file are self-explanatory. In my
final configuration, I did not have any pins left, so if you make
changes to the sensor configuration you have to change some of the pin
assignments.

If you have less than 5 taps, you can change the numscales variable to
the number of taps you have. If you have less than 4 taps you may want
to modify the display.

The 64 colors are also defined in this file. The color names are based
upon the RGB values for the color. I had to modify some of the names
because they were too long or conflicted with other constants.

## Keg Monitor

The Keg Monitor file is the main module. It has the libraries used with
an explanation for each one. There are two libraries that I wrote myself
included. \<HX711_Single_Clk.h\> and \<DHTSimple.h\>. These libraries
are available on my GitHub site. \<HX711_Single_Clk.h\> library drives
all the scales on a single clock reducing number of pins.
\<DHTSimple.h\> is a non-blocking DHT sensor reading library. Most
libraries block interrupts when reading the DHT sensor which causes the
display to flicker each time the sensor is read.

The main loop checks for input in Serial 0 (Serial Monitor interface),
Serial 2 the interface to the Wi-Fi board, the keyboard, and tasks. You
can type in commands on the Serial 0 interface. The tasks run every 3
seconds, 10 seconds, and every minute. The 3 second task only runs when
calibrating a keg. The 10 second task is for reading the freezer
temperature and reading the scale values. The 1-minute tasks are for
display update and sending data to the Wi-Fi board.

### Files

The files folder reads and writes the configuration information in a
file name config.txt. This file is in the “data” folder per the Arduino
standard. The configuration file must be uploaded to the ESP32 board for
the program to run. There are several places where you can find
instructions on setting up a file system and uploading files.
/<https://randomnerdtutorials.com/install-esp32-filesystem-uploader-arduino-ide/>.
I chose the LittleFS because it is small and reliable.

This file stores all the important information on your system. Open the
file to see this information. The file is only updated when you use the
Save command.

## Temperature

This file does all temperature sensor processing. It initializes the
sensors, reads the temperatures, adds the bias, checks the temperatures,
runs a moving average on the sensor being used and turns the freezer on
and off. The temperature checking depends upon the number of sensors
installed.

## Keyboard

The keyboard file processes the keys that are pressed. Depending on what
display is currently being shown, the keys are processed differently.

## Commands

The command file processes the input commands.

## Display

The display file processes the 4 displays. There are the Main Display,
Command Display, Alarms Display and Scales Display.

The alarm display shows the current active alarms. Exiting this display
clears all alarms.

The scales display is used to check and troubleshoot the keg scales.
There are two options: raw values and delta values. The raw values are
the quanta values currently being read. The values should be similar
from reading to reading. The delta values are the difference between two
readings.

## Scales

The scale file reads the scales, checks the read values, calibrates the
scales, calculates the number of glasses left in each keg and does the
time-of-day calculations. The only thing the time of day is used for is
to calculate the number of days the beer has been kegged.

## Wi-Fi

This file has the Wi-Fi initialization and Time of day functions

## CO2

This file has the CO2 functions to read the pressure transducer and
operate the solenoid valve.

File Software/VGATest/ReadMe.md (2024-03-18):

# VGA Test

This software will test the VGA interface. Every VGA monitor is a little
different so if you want the best colors, you can run this test to make
sure your hardware is set up optimally.

## Main Display

The following figure is a sample of the Main Display.



The picture is not great because of the video refresh rate. The top
three rows show the Red, Green, and Blue primary colors. The goal is to
have as much differentiation between the row of colors. If you can not
tell the difference between the left, middle and right color you need to
check your connection or change the resistor values. You can move the
outputs (i.e. Red1 and Red0) to a breakout board and switch in different
resistor values. I used 100-ohm resistors to get a good differentiation.
You can also use a potentiometer.

The bottom part of the display shows the possible 64 colors that can be
displayed.

Type in ‘c’ in the Serial Monitor and it will take you to another
display. The following is a sample of the display:

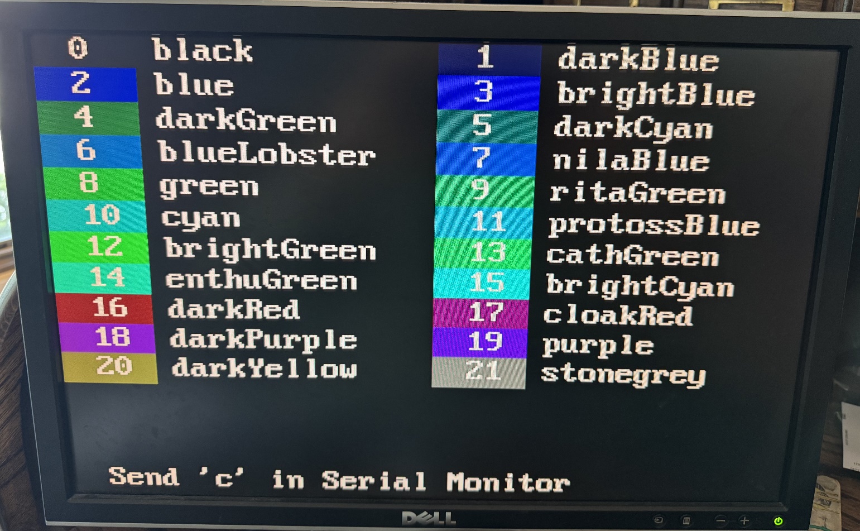
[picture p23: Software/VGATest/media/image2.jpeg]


The display shows the first 21 colors. The color (with the number inside
the color) followed by the color name. You can use the number or the
name to select the color. The following two images show the displays as
type ‘c’ in the Serial Monitor.

You can scroll through the three displays to see all the colors, to
decide which ones you want to use.

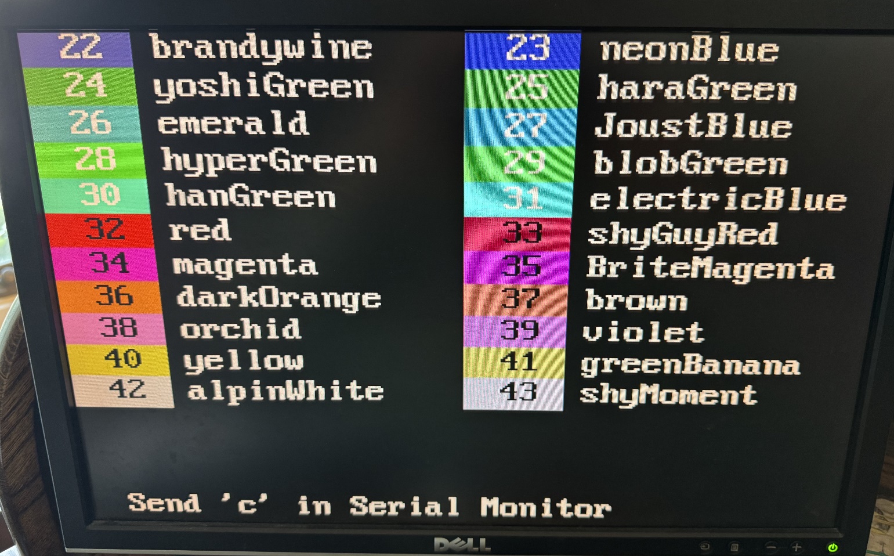
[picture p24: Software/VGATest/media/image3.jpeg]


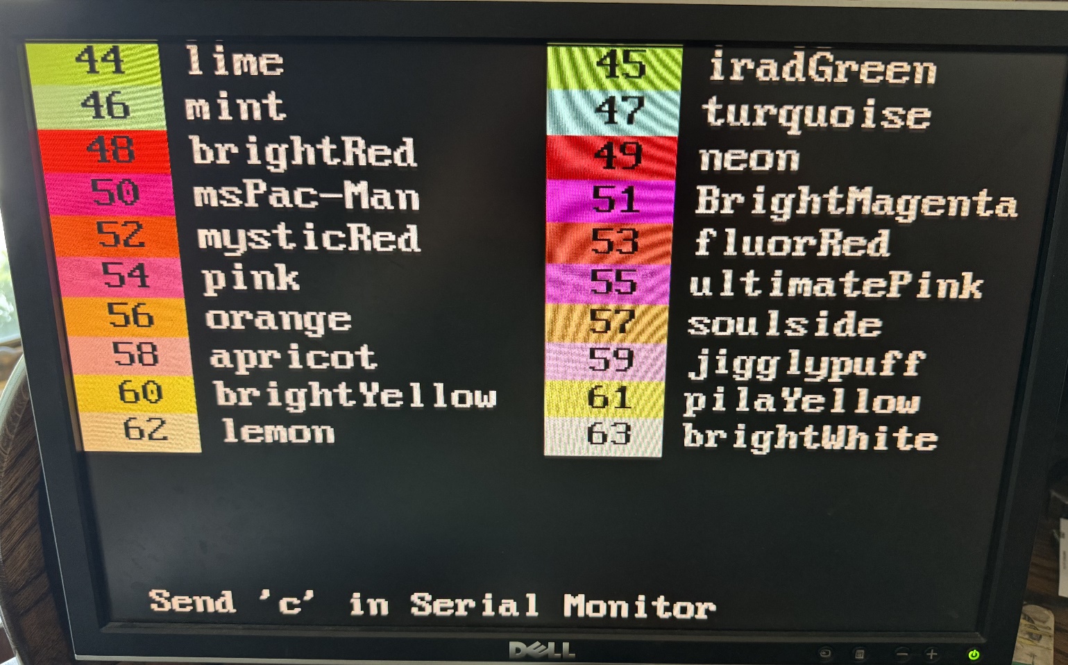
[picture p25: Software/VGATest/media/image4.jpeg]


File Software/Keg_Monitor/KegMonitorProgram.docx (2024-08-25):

# Keg Monitor Program

The Keg monitor program controls the freezer temperature, measures how many glasses of beer are available and provides a display with all the beer information you need.

The program runs on the FREENOVE ESP32-WROOM development board (Keg_Monitor_RevX.X.ino). Arduino compile information is included on the first line of the file.

The program also interfaces to a Wi-Fi board via a serial interface. You can use the program without this interface, but you will not be able to send emails or text messages if something is wrong. You can manually input the time of day to get the number of days the beer has been kegged.

The program display is a standard VGA display. I set the resolution to 40 characters by 15 lines, so it is easy to read from a distance. The following section describes the display.

# Main Display Overview

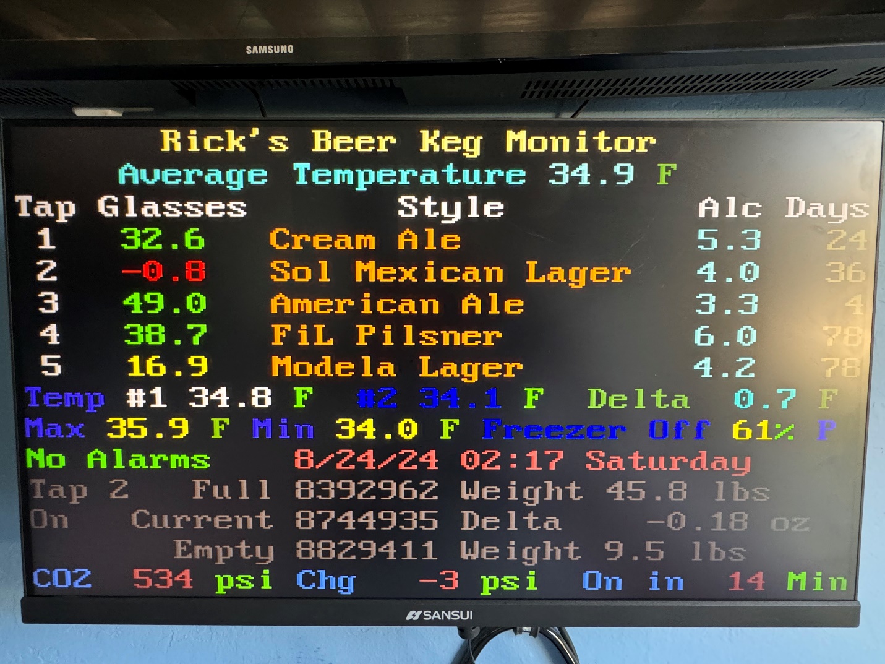
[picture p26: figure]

The first line is the Name of your system. I called mine Rick’s Beer Keg Monitor.

The second line is the average temperature. This is the average of 180 samples or 30 minutes.

The third line is the titles for the columns. The first column is the Tap number, the second column is the number of glasses remaining, the third column is the name and style of the beer, the fourth column is the percentage of alcohol, and the last column is the number of days the keg has been in freezer. The Glasses column changes colors depending on how many are left. Less than 30 is yellow and less than 10 is red.

The 9th line is the current temperatures. The highlighted temperature is the sensor currently being used.

The 10th line displays alarms and time of day. If there are not any alarms the display will show “No Alarms” in green. If there are alarms the display will show the number of alarms in red. Next to the alarms is the time of day. If the Wi-Fi module is connected the time of day is automatically displayed. If the area is blank, you can manually input the time of day.

The next three lines provide scale information. The first line is Tap number, the scale quanta value for a full keg and the weight of the keg when it was full. The next line shows the current quanta value and the change in ounces between two consecutive readings. If the scale is working properly this should be a small number, unless you are pouring a beer. The last line shows the empty scale (nothing on the scale) quanta value and the weight of an empty keg.

The last line is the CO2 status information. The first field is the current CO2 pressure. The next field is the change in pressure during the last hour. If the change is greater than 100 psi you may have a leak. The last field is how many minutes before the CO2 valve turns on agan.

With the main display being displayed pressing a key will have the following effect:

- Key a – Displays the current alarms. Pressing the Esc key will clear the alarms and return you to the main display.
- Key 1-5 – Pressing a number key will display the information for the appropriate tap in the bottom three rows. If you select the tap before you pour you can watch the ounces change.
- Key c – Clears the Minimum, Maximum and average temperatures.
- Key s – Opens the scale display window.
- Key p – Opens the CO2 plot display window
- Key Esc – Opens up the command menu.

## Command Menu


With this display you type the command to execute. As you type, the letters appear on the bottom of the display in the box. You can hit backspace to clear what you typed. To exit this display hit the Esc key.

The first five lines are for entering keg information. Type the Tap number and the information. The information is alcohol percentage, Style or name of beer, date the beer was kegged or installed in the freezer and the weight of an empty keg.

The 5th line is for calibrating an empty keg and full keg. If there is not anything on the scale the main display should show the number of glasses at about minus 13. If not calibrate the scale with a weight of 0. Put the full keg on the scale and enter the weight of the full keg to calibrate.

The next line sets the CO2 valve rate. 0 turns it on continuously and 99 turns it off.

The nest line sets either the primary or secondary relay.

Save to file, saves the current information to file. Don’t forget to Save when you have input information correctly.

Date is used to input the current date and time when you don’t have the Wi-Fi board connected.

The “Temp i Bias” line is to input the bias on the temperature sensors. The line shows the current bias value.

The Goal is the temperature you want your freezer to be. The DHT sensors can have a bias. I have had some sensors that had a bias up to 2 degrees. Before you set the goal too low make sure the bias and temperature are correct. Freezing beer is BAD! I found that 36 degrees is safe, and the beer still tastes nice and cold. Refrigerators are normally 40 degrees.

## CO2 Saver

When you press ‘p’ on the main display the following plot is displayed.


The top row shows the current average pressure, and the slope of the line fit to the raw data. The Rate is the current on rate.

The next line is the previous mean and slope. The last field is when the CO2 valve will turn on.

The rest of the display is the plot. The left is the X-axis in psi and the bottom is the y-axis in number of samples. The green values and line are the linear regression fit the raw data. The white is the raw data.

## Setup

All the setup is done by editing the “Constans.h” file. In my configuration all the available GPIO pins are used. I use two MCP9808 temperature sensors that use the SCLpin and SDApin. If you want to use different temperature sensors you need to change the pin numbers. So for example, if you are using two DHT Type 2 sensors you need to change the DHT1Pin to 13 and the DHT2pin to 14 and change SCLpin to -1 and SDApin to -1. You have to keep all the pin names for the program to compile.

Another example, if you are not using the CO2 Saver, you set CO2Saver to false. Now pin 0 and pin 35 are available to use, but you have to set CO2ValvePin to -1 and CO2PressurePin to -1.

If you are using Wi-Fi to get time of day, you have to set ssid to the name of your Wi-Fi network and password to the password of your network. If you don’t live on the west coast you have to change the gmtOffset_sec to your time zone.

## Software Files

The software is divided into files. The files contain functionally similar functions.

### “Constants.h”

This file contains the temperature sensor configuration information, GPIO pin assignments, color constants, alarm numbers and other global constants. I made this a separate file to reduce clutter in the main program. I think the comments in the file are self-explanatory. In my final configuration, I did not have any pins left, so if you make changes to the sensor configuration you have to change some of the pin assignments.

If you have less than 5 taps, you can change the numscales variable to the number of taps you have. If you have less than 4 taps you may want to modify the display.

The 64 colors are also defined in this file. The color names are based upon the RGB values for the color. I had to modify some of the names because they were too long or conflicted with other constants.

## Keg Monitor

The Keg Monitor file is the main module. It has the libraries used with an explanation for each one. There are two libraries that I wrote myself included. <HX711_Single_Clk.h> and <DHTSimple.h>. These libraries are available on my GitHub site. <HX711_Single_Clk.h> library drives all the scales on a single clock reducing number of pins. <DHTSimple.h> is a non-blocking DHT sensor reading library. Most libraries block interrupts when reading the DHT sensor which causes the display to flicker each time the sensor is read.

The main loop checks for input in Serial 0 (Serial Monitor interface), Serial 2 the interface to the Wi-Fi board, the keyboard, and tasks. You can type in commands on the Serial 0 interface. The tasks run every 3 seconds, 10 seconds, and every minute. The 3 second task only runs when calibrating a keg. The 10 second task is for reading the freezer temperature and reading the scale values. The 1-minute tasks are for display update and sending data to the Wi-Fi board.

### Files

The files folder reads and writes the configuration information in a file name config.txt. This file is in the “data” folder per the Arduino standard. The configuration file must be uploaded to the ESP32 board for the program to run. There are several places where you can find instructions on setting up a file system and uploading files. /https://randomnerdtutorials.com/install-esp32-filesystem-uploader-arduino-ide/. I chose the LittleFS because it is small and reliable.

This file stores all the important information on your system. Open the file to see this information. The file is only updated when you use the Save command.

## Temperature

This file does all temperature sensor processing. It initializes the sensors, reads the temperatures, adds the bias, checks the temperatures, runs a moving average on the sensor being used and turns the freezer on and off. The temperature checking depends upon the number of sensors installed.

## Keyboard

The keyboard file processes the keys that are pressed. Depending on what display is currently being shown, the keys are processed differently.

## Commands

The command file processes the input commands.

## Display

The display file processes the 4 displays. There are the Main Display, Command Display, Alarms Display and Scales Display.

The alarm display shows the current active alarms. Exiting this display clears all alarms.

The scales display is used to check and troubleshoot the keg scales. There are two options: raw values and delta values. The raw values are the quanta values currently being read. The values should be similar from reading to reading. The delta values are the difference between two readings.

## Scales

The scale file reads the scales, checks the read values, calibrates the scales, calculates the number of glasses left in each keg and does the time-of-day calculations. The only thing the time of day is used for is to calculate the number of days the beer has been kegged.

## Wi-Fi

This file has the Wi-Fi initialization and Time of day functions

## CO2

This file has the CO2 functions to read the pressure transducer and operate the solenoid valve.

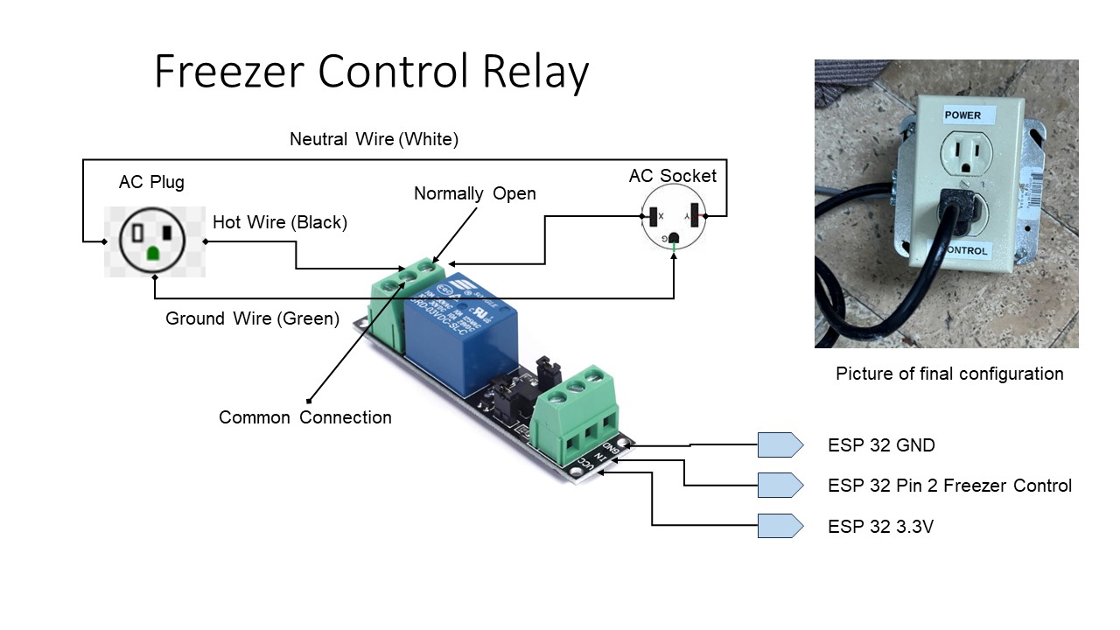
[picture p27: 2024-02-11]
Hardware/FreezerControl/FreezerControl.jpg

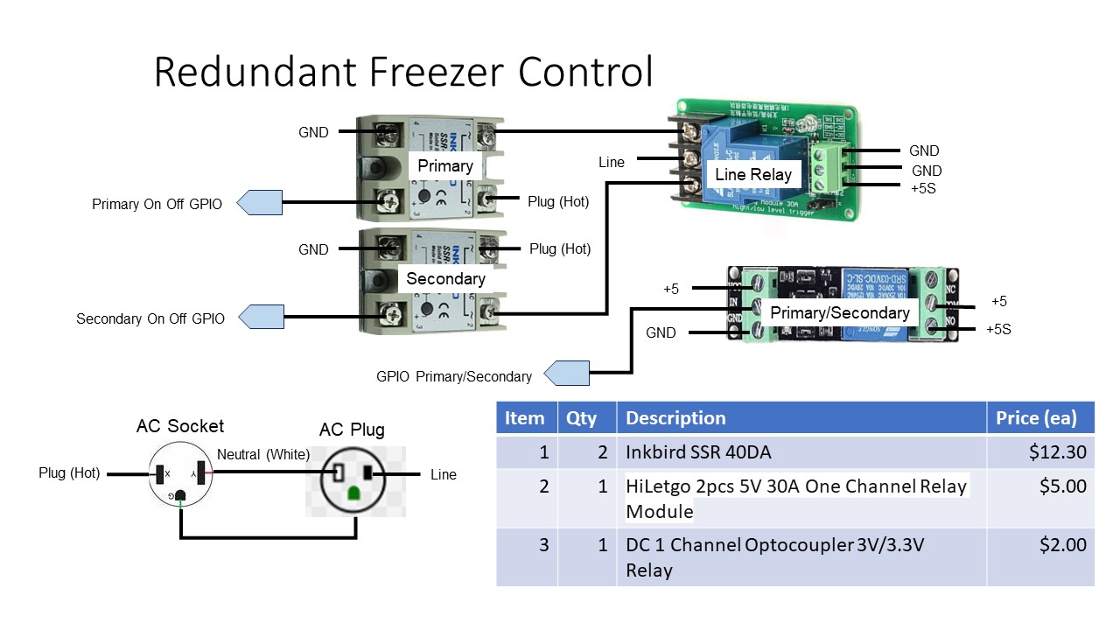
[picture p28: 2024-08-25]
Hardware/FreezerControl/RedundantRelay.jpg

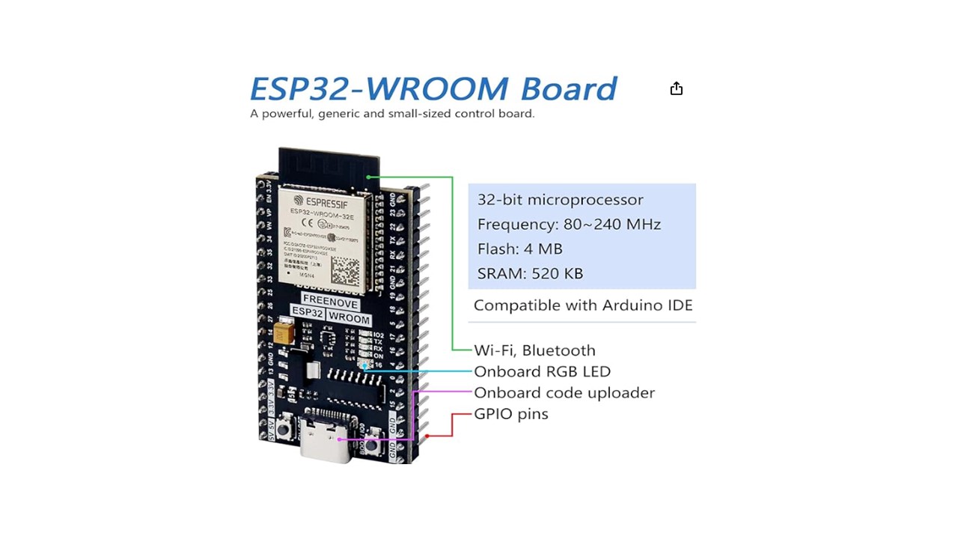
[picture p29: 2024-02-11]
Hardware/ESP32_WROOM/ESP32_WROOM.jpg

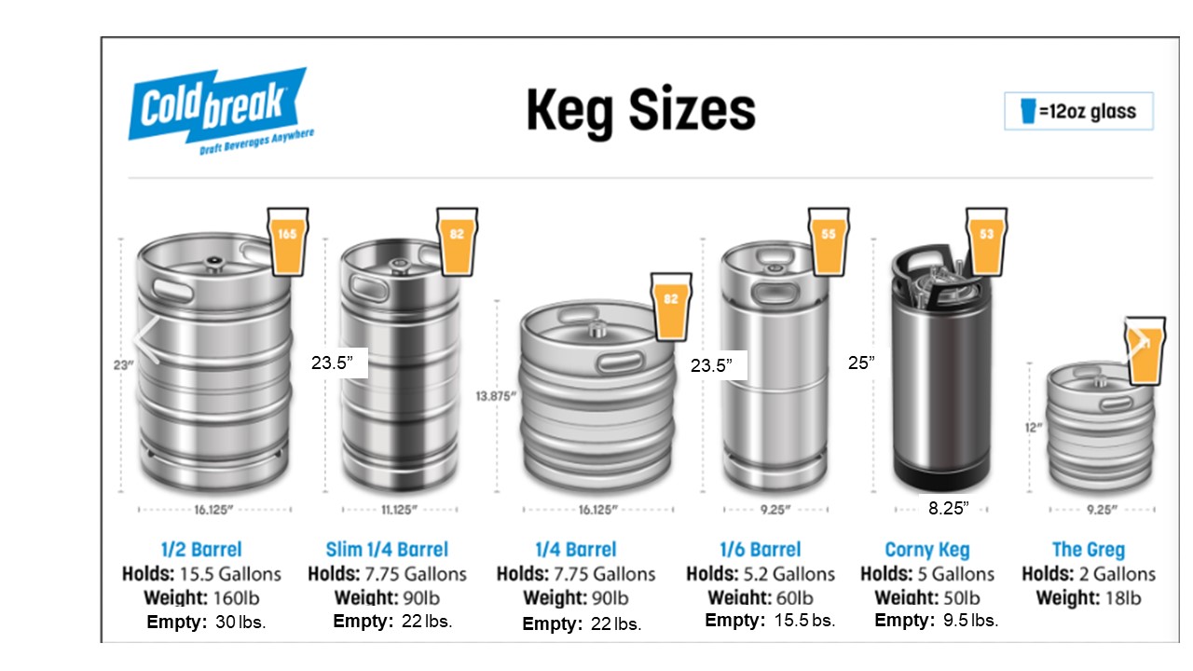
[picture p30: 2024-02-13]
Hardware/Scale_Design/KegSizes.jpg

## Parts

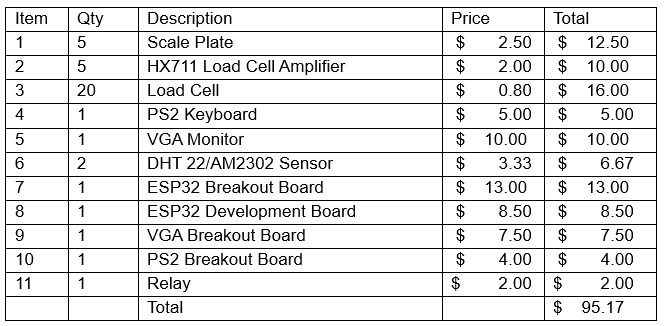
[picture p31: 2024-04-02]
BOM.jpg

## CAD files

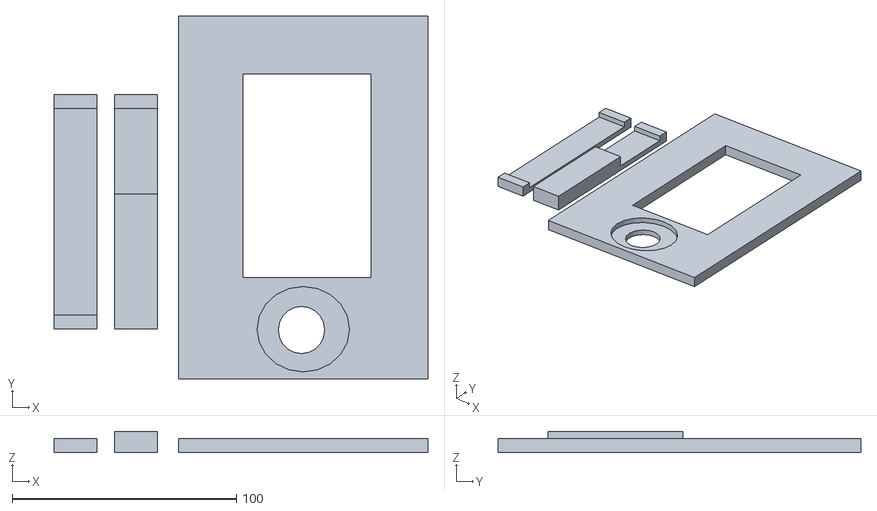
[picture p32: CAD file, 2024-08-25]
Hardware/Electrical Box Model/elec box lid.stl
166.7 x 161.9 x 9.52

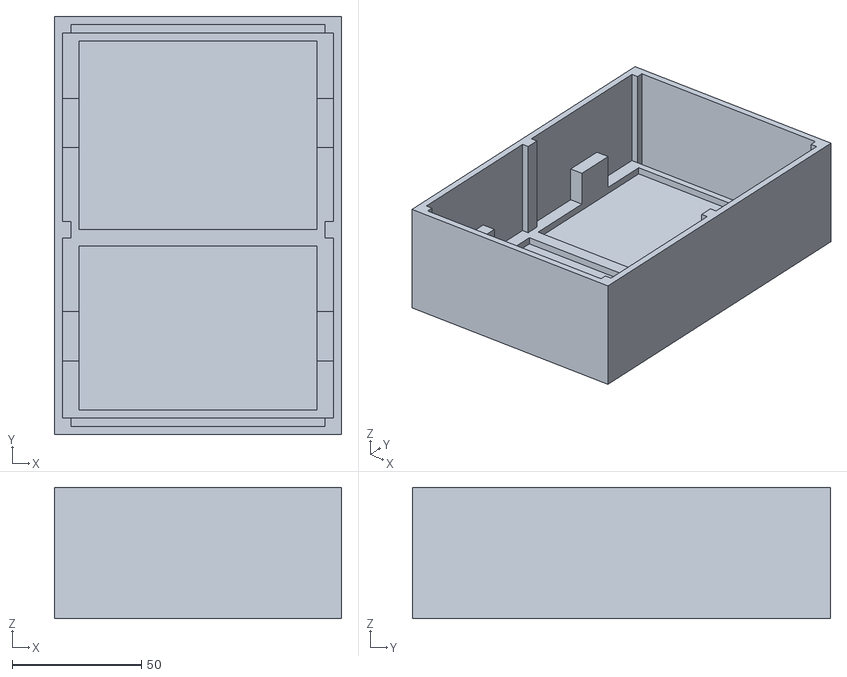
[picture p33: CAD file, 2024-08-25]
Hardware/Electrical Box Model/Elec Box.stl
111.1 x 161.9 x 50.8

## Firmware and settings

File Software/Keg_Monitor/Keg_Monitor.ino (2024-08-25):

/* Use ESP32 WROOM Dev Module* Huge APP, Arduino Core 1, Events Core 0 
   Set Serial Monitor to 9600 Baud */
#include <Arduino.h>
#include <WiFi.h>                 //Wi-Fi Library
#include <TimeLib.h>              //Time Library
#include <Wire.h>                 //Library for I2C Interface
#include "mcp9808.h"              //MCP9808 Library 
#include "fabgl.h"                //VGA Monitor and Keyboard library
#include "FS.h"                   //File System Library (required for LittleFS)
#include "LittleFS.h"             //Little File System Library  
#include <HX711_Single_Clk.h>     //HX711 Library (Custom Library requires download and Install)   
#include <DHTSimple.h>            //DHT Sensor Library (Custom Library requires download and Install)
#include <OneWire.h>              //Arduino Library for One Wire devices
#include <DallasTemperature.h>    //DS18B20 device library "Arduino-Temperature-Control-Library"
#include "Constants.h"            //Configuration, Constants and Pin Numbers

boolean ScalesConnected = true;                 // used for debuging
boolean const printSerial = false;
int ptr = 0;

/* constructors */
fabgl::VGAController VGAController;
Canvas cv(&VGAController);
fabgl::PS2Controller     PS2Controller;
HX711O Scale(numscales);                     //constructor number of devices and size of array passed
MCP9808 Sensor1(0x18);
MCP9808 Sensor2(0x19);
MCP9808 Sensor3(0x1A);
DHTSimple dht1(DHT1Pin, DHTType);
DHTSimple dht2(DHT2Pin, DHTType);
DHTSimple dht3(DHT3Pin, DHTType);
OneWire oneWire(ONE_WIRE_BUS);                               // Setup a oneWire instance to communicate with any OneWire devices
DallasTemperature sensors(&oneWire);                         // Pass our oneWire reference to Dallas Temperature
DeviceAddress DS18B20Temp1, DS18B20Temp2, DS18B20Temp3;      // arrays to hold device addresses

/* Filenames */
const String ConfigFN = "/config.txt";                    /* Configuration file name */ 

/* File Variables */
float EmptyKW[maxscales];                               /* Empty Keg Weight */
float FullKegWeight[maxscales];                         /* Full Keg Weight */
long FullKeg[maxscales];                                /* Full Keg Quanta */
long EmptyKeg[maxscales];                               /* Empty Keg (no keg) Quanta */
String KeggedDate[maxscales];                           /* Date Kegged mm/dd/yy format */
float Alcohol[maxscales];                               /* Percent Alcohol */
String BeerNames[maxscales];                            /* Titles for each Tap */ 
int DaysKegged[] = {0, 0, 0, 0, 0};                     /* Number of days the beer has been in the keg */
int Tempgoal = 34;                                      /* Desired Freezer Temperature */
int MaxTemp;                                            /* Maximum temp that is possible */
int MinTemp;                                            /* Minimum temp that is possible */
float HighTemp;                                         /* Maximum temperature observed */
float LowTemp;                                          /* Lowest temperature observed */

/* Temperature and Freezer Global Variables */
float Temperature[] = {0, 0, 0, 0};           /* Average Temperature, Sensor #1, Sensor #2, Sensor #3 */
float TempBias[4];                             /* Delta (#1-#2), Sensor #1 Offset, Sensor #2 Offset, Sensor #3 Offset */
int numTS = 0;
int UsingSensor = 1;

unsigned long Tensecond;
unsigned long OneMinuteTT;
unsigned long Threesecond;
unsigned long curtime = 0;                             /* Current running time in millis */

/* CO2 Variables */
#define CO2BufLen 290             //Number of samples to Plot
long CO2Pressure = 0;             //current pressure psi
long CO2Rate = 60;                //On Rate in minutes
unsigned long CO2OnTime = 30000;  //CO2 Next On Time
unsigned long CO2Reset = 0;       //Reset Rate back to 60 minutes
int MaxPressReading = 0;          //CO2 Maximum Pressure Reading
int MinPressReading = 0;          //CO2 Minimum Pressure Reading
int CO2BufPtr = 0; 
int CO2PressureBuf[CO2BufLen];
int CO2PressureChg = 0;
float offset = 0; float prevOffset = 0;
float slope = 0;  float prevSlope = 0;

int CurrentTap = 1;
float GlassesLeft[] = {5.0, 10.0, 15.0, 20.0, 30.0};
boolean TempAvailFlag = true;
boolean FreezerState = false;
int FreezerOnPercent = 0;
String InputError = "";
String InputResults = "";
String AlarmStr = "";
int AlarmCnt = 0;
long AlarmFlag = 0;
int ScaleClk = ScaleClkPin;
int ScaleOut[] = {ScaleOut0Pin, ScaleOut1Pin, ScaleOut2Pin, ScaleOut3Pin, ScaleOut4Pin};
String DisplayUpdateStr = "";

/* ---------------------------  Setup --------------------------------------------- */
void setup()
{
/* Setup VGA */  
  PS2Controller.begin(PS2Preset::KeyboardPort0);
  //VGAController.begin(GPIO_NUM_22, GPIO_NUM_19, GPIO_NUM_5, GPIO_NUM_23, GPIO_NUM_15);
  // Use GPIO 22-21 for red, GPIO 19-18 for green, GPIO 5-4 for blue, GPIO 23 for HSync and GPIO 15 for VSync
  //VGAController.begin(GPIO_NUM_22, GPIO_NUM_21, GPIO_NUM_19, GPIO_NUM_18, GPIO_NUM_5, GPIO_NUM_4, GPIO_NUM_23, GPIO_NUM_15);
  VGAController.begin();
  VGAController.setResolution(QVGA_320x240_60Hz);
  delay(500);
  cv.setPenColor(Color::Yellow);
  cv.setBrushColor(Color::Black);
  cv.selectFont(&fabgl::FONT_8x16);

  Serial.begin(115200);
  delay(500);  // avoid garbage into the UART

  const char myVer[] = __DATE__ " @ " __TIME__;
  DisplayPrint("Build: " + String(myVer));
  DisplayPrint("VGA Setup Complete");

  pinMode(CO2ValvePin, OUTPUT);
  digitalWrite(CO2ValvePin, LOW);
  if (CO2OnlyFlag) CO2OnlyLoop();

/* Intialize WiFi */
 if (InitWiFi()) {
    DisplayPrint("Connected to WiFi! " + String(RSSIlvl,1) + " dBm");
  }  
  else {
    DisplayPrint("Failed to Connected to WiFi!");
  }

/* Setup Pin Modes */
  pinMode(PrimaryOnOffPin, OUTPUT);
  pinMode(SecondaryOnOffPin, OUTPUT);
  pinMode(PrimarySecondaryPin, OUTPUT);
  digitalWrite(PrimarySecondaryPin, Primary);
  digitalWrite(PrimaryOnOffPin, LOW);
  digitalWrite(SecondaryOnOffPin, LOW);
  pinMode(ScalePowerPin, OUTPUT);
  digitalWrite(ScalePowerPin, HIGH);
  ScaleOnFlag = true;
  DisplayPrint("Hardware Pins Set");

/* Set Time from NTP Service */
  DisplayPrint("Getting Current Time");
  delay(1000);
  if (!SetRTCTime()) {
    DisplayPrint("Failed to obtain Time");
    DateTime = "No Time Available";
    MidNightReset = DAYSECONDS;
  }
  else {
    TimeSet = true;
    DateTime = DateTimeStr();
    DisplayPrint("Current Time is " + DateTime);
    MidNightReset = (DAYSECONDS - (hour()*3600 + minute()*60) + second()) * 1000 - millis();
  }  

/* Get Initial Temperature readings */ 
  int GoodTS = InitTempSensors();
  if (GoodTS == 0) {
    DisplayPrint("No good Temperature Sensors!");
  }
  else  {
    DisplayPrint(String(GoodTS) + " out of " + String(numTS) + " Temperature Sensors are good");
  }
  
/* Start LittleFS */
  if(!LittleFS.begin()){                                                         /* Is File System OK? */ 
    Serial.println("An Error has occurred while mounting LittleFS");
    DisplayPrint("File system is corrupted");                                    /* Set Critical Status */
    delay (1000);
    while(1);
  }
/* Get stored data from Config File */  
  else {
    listDir(LittleFS, "/", 1);                                                   /* List Files in FS */
    if (ReadConfigData()) {                                                      /* Read Configuration data from file */
      Serial.println("Displaying Configuration Variables");
      PrintConfigData();                                                         /* display data read */
      DisplayPrint("Config Data Good");                                        /* Set Good Status */
    }
    else {                                                                       /* Configuration data corrupted */
      DisplayPrint("Config Data read error");                                         /* Set Critical Status */
      delay(1000);
      while(1);
    }
  }
  /* Intialize and Start Scales */
  if (ScalesConnected) {
    InitializeScales();
  }  
  else {
    DisplayPrint("Scales not Connected");
  }

  DisplayPrint("Setup Complete");
  delay(5000);

  cv.clear();
  ClearDisplayUpdateStr();
  DisplayUpdate();

/* Stagger Tasks times to reduce CPU load  */
  curtime = millis();
  Tensecond = curtime + TENSECONDMILS + 200;
  OneMinuteTT = curtime + MINUTEMILS + 2500;
  CO2OnTime = curtime + TENSECONDMILS*3 + 600;
  ScreenSaverStartTime = curtime + ScreenSaverStart;
}
/* ---------------------------  Main Loop  --------------------------------------------- */
void loop()  {
  curtime = millis();

/* Check if a key has been pressed */
  auto keyboard = PS2Controller.keyboard();
  if (keyboard->virtualKeyAvailable()) {
    VirtualKeyItem item;
    if (keyboard->getNextVirtualKey(&item)) {
      char key = item.ASCII;
      if(item.down == 0) {                                                 /* Key Released */
        //Serial.print(key); Serial.println(" key Pressed");
        ProcessKey(key);
      }
    }
  }      

/* 10 Second Tasks */  
  if (curtime > Tensecond) {                                                     
    Tensecond = Tensecond + TENSECONDMILS;
    GetTemperature();
    if (ScalesConnected) ProcessScaleValues();
    ReadCO2Pressure();
  }  
/* 1 Minute Tasks */  
  if (curtime > OneMinuteTT) {         
    OneMinuteTT = OneMinuteTT + MINUTEMILS;
    if (curtime > ScreenSaverStartTime) {
      if (ScreenSaverOn == false) {
        cv.clear();
        ScreenSaverOn = true;
        Serial.println("Screen Saver is On");
      }  
    }
    if (TimeSet) DateTime = DateTimeStr();
    CalcDaysKegged(DateTime);
    if(DisplayMode == Normal) DisplayUpdate();
    if(curtime > MidNightReset) ESP.restart();
  }
/* CO2 Control Tasks */  
  if (curtime > CO2OnTime) {         
    CheckCO2();
  }
/* Check if Scale is Ready */  
  if (ScaleOnFlag == false) {
    if (curtime > ScaleOnTime) {
      if (digitalRead(ScalePowerPin) == HIGH) {
        ScaleOnFlag = true;  
      }
      else {
        digitalWrite(ScalePowerPin, HIGH);
        ScaleOnTime = curtime + 1000;                            //Scale not ready for 450 ms to set flag to true
      }
      
    }
  }
}

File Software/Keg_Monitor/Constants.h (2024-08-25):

/* Temperature Sensor Configuration */
/* You must have at least one sensor, a maximum of 2 of each type of sensor are allowed */
#define MCPSensors 2          //Number of MCP9808 Sensors SCLpin and SDApin must have valid pin numbers
#define DS18B20Sensors 0      //Number of DS18B20 Sensors ONE_WIRE_BUS must have a valid pin number
#define DHTSensors 0          //Number of DHT Sensors 
#define DHTType 2             //DHT11 is 1, All others 2 (DHT21, DHT22, AM2301, AM2302) 
#define DHT1Pin -1            //Pin must be changed if DHT sensor is used 
#define DHT2Pin -1            //Pin must be changed if DHT sensor is used
#define DHT3Pin -1            //Pin must be changed if DHT sensor is used
#define ONE_WIRE_BUS -1       //Pin must be changed if DS18B20 Sensors are used

#define CO2OnlyFlag false
#define numscales 5                      /* Number of Scales and taps */
#define numColors 64                     /* Number of display colors 8 or 64.  8 usese 5 wires and 64 uses 8 wires */

/* Pin assignments */
#define CO2ValvePin 0                   // CO2 Solenoid On/Off
#define TXD0 1                          //UART 0 TX, Debug output at boot
#define ScalePowerPin 2
#define RXD0 3                          //UART 0 RX, High at boot, UART 0 Rx
#define Blue0Pin 4
#define Blue1Pin 5
#define ScaleOut0Pin 12                  //boot fails if pulled high
#define SCLpin 13                        
#define SDApin 14                        //outputs PWM signal at boot  
#define VSyncPin 15                      //outputs PWM signal at boot 
#define SecondaryOnOffPin 16             //UART 2 RX
#define PrimaryOnOffPin 17               //UART 2 TX
#define Green0Pin 18
#define Green1Pin 19
#define Red0Pin 21                        //Default SDA
#define Red1Pin 22                        //Default SCL
#define HSyncPin 23
#define ScaleOut4Pin 25              
#define PrimarySecondaryPin 26
#define ScaleClkPin 27
#define KeyboardDataPin 32
#define KeyboardClkPin 33
#define ScaleOut3Pin 34
#define CO2PressurePin 35                //Receive Only
#define ScaleOut1Pin 36                   //Receive Only VP
#define ScaleOut2Pin 39                   //Receive Only VN

/* Time Variables */
const char* ntpServer = "pool.ntp.org";
const char* ntpServer2 = "time.nist.gov";
const long  gmtOffset_sec = -480*60;                       // Los Angeles Time Zone -8 hours
const int   daylightOffset_sec = 3600;                     // Set to 0 if you don't have DST
unsigned long MidNightReset = 0;
String DateTime = "";
boolean TimeSet = false;

/* Scale Variables */
#define maxscales 5
#define Gain 128
long ScaleReadings[maxscales];
long ScaleValues[maxscales];
long PrevScaleValues[maxscales];
char ScaleDisp; 
float CalWeight = 0;
unsigned long ScaleOnTime = 0;
boolean ScaleOnFlag = false;

/* WiFi Variables */
String IPaddr = "";                                     /* IP Address */ 
float RSSIlvl = 31.0;                                   /* Current RSSI level in dBm */
boolean WiFiflag = false;                               /* Flag if WiFi is connected */
const char* ssid     = "Network_Name";                     //Wi-Fi network Name
const char* password = "PASSWORD";                      //Password to log on to your internal Wi-Fi network  

/* Common global defines */
#define On 1
#define Off 0
#define MINUTES3 1000*60*3
#define MINUTES10 1000*60*10
#define MINUTES30 1000*60*30
#define DAYSECONDS 3600*24
#define THREESECONDMILS 1000*3
#define TENSECONDMILS 1000*10
#define MINUTEMILS 1000*60
#define HOURMILS 1000*3600
#define EpochYear 2023
#define DHTTYPE DHT22     // DHT 22  (AM2302), AM2321
#define EpochUnix 1704096000  //Unix Time Jan 1, 2023 00:00
#define TimeZoneOffset -8  //Standard Time Zone Offset Hours  Los Angeles is 8 hours
#define EpochYear 2024
#define MaxDeltaTemp 3
#define MaxStableCnt 9
#define Primary LOW
#define Secondary HIGH
#define TEMPERATURE_PRECISION 9

/* Display Variables */
#define Command 1
#define Alarm 2
#define Scales 3
#define Normal 4
#define Plot 5
#define ScreenSaverStart HOURMILS                  //2*HOURMILS
unsigned long ScreenSaverStartTime = 0;
boolean ScreenSaverOn = false;
int DisplayMode = Normal;

/* Alarm Flag bits */
#define Alarm0 0  //Serial2: Invalid Scale number 
#define Alarm1 1  //Scale TimeOut
#define Alarm2 2  //Scale Not Connected 
#define Alarm3 3  //Available
#define Alarm4 4  //Temp Sensors don't match
#define Alarm5 5  //Temp Sensor Unreasonable
#define Alarm6 6  //MCP Sensor Read Error
#define Alarm7 7  //All Temp Sensors Bad
#define Alarm8 8  //DHT Temp Sensor Read Error
#define Alarm9 9  //Reset HX711 
#define Alarm10 10  //Freezer too cold switched to Secondary 
#define Alarm11 11  //Freezer too hot switched to Secondary 
#define Alarm12 12  //DS18B20 Temperature Read Error
#define Alarm13 13  //CO2 Reading below Minimum PSI
#define Alarm14 14  //CO2 Tank Pressure is Low, Replace Tank
#define Alarm15 15  //CO2 Reading below 100 PSI, Leak
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

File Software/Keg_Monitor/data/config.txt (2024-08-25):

Empty_Keg_Weight:           8.80,       9.50,       9.40,       9.80,      15.00,
Full_Keg_Weight:            47.0,       45.8,       48.2,       43.8,       65.0,
Full_Keg_Raw:            7825374,    8392962,    7950880,    8877161,    7699734,
Empty_Keg_Raw:           8300654,    8829411,    8425063,    8433264,    8299932,
Date_Kegged:             7/31/24,    7/19/24,    8/20/24,     6/7/24,     6/7/24,
Alcohol:                     5.3,        4.0,        3.3,        6.0,        4.2,
Titles:              Cream Ale, Sol Mexican Lager, American Ale, FiL Pilsner, Modela Lager, 
Temp_Bias_goal:       -1.0, 0.0, 0.0, 35, 
Validation:         19772, 

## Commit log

2024-03-05 First Upload
    [config.txt]
2024-04-02 publish Wi-Fi Display program
    [config.txt]
2024-08-25 Added CO2 Saver
    [Elec Box.stl, config.txt, elec box lid.stl]
2024-08-25 Fixed Scale Change Problem
    [Keg_Monitor.ino]
